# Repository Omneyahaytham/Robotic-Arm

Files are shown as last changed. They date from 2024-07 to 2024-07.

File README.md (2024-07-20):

# Robotic-Arm
Simulation of a robotic arm designed on solidworks and simulated on MATLAB and ROS. given a specific points that end effector must follow (Path planning)
used forward and inverse kinematics to minimize the error

Note:
you need robotic toolbox for this project.
need to know how to export solidwork design on matlab.

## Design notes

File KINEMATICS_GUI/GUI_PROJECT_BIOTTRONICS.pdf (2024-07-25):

### Mechatronics and robotics

Ahmed Mohamed Kotp | 7543
Omneya Haytham Mohamed | 7717
Faress Ahmed Mohamed Amin | 7925

# INTRO TO BIOTRONICS ASSIGNMENT

# GUI Assignment

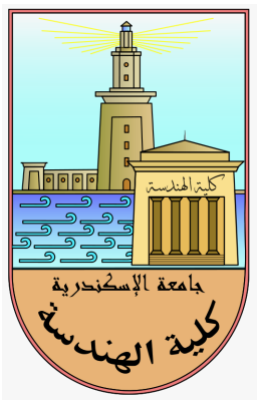
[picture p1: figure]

## GUI-Based Serial Link Kinematics Solver

## Objective:

The objective of this assignment is to develop a graphical user interface (GUI) application in

MATLAB for solving serial link kinematics problems. Students will design a user-friendly

interface that allows users to input serial link configurations and select the type of problem

(forward or inverse kinematics). They will then implement algorithms to solve the selected

problem type and display the final pose of the serial link robot.

### 1. GUI Design:

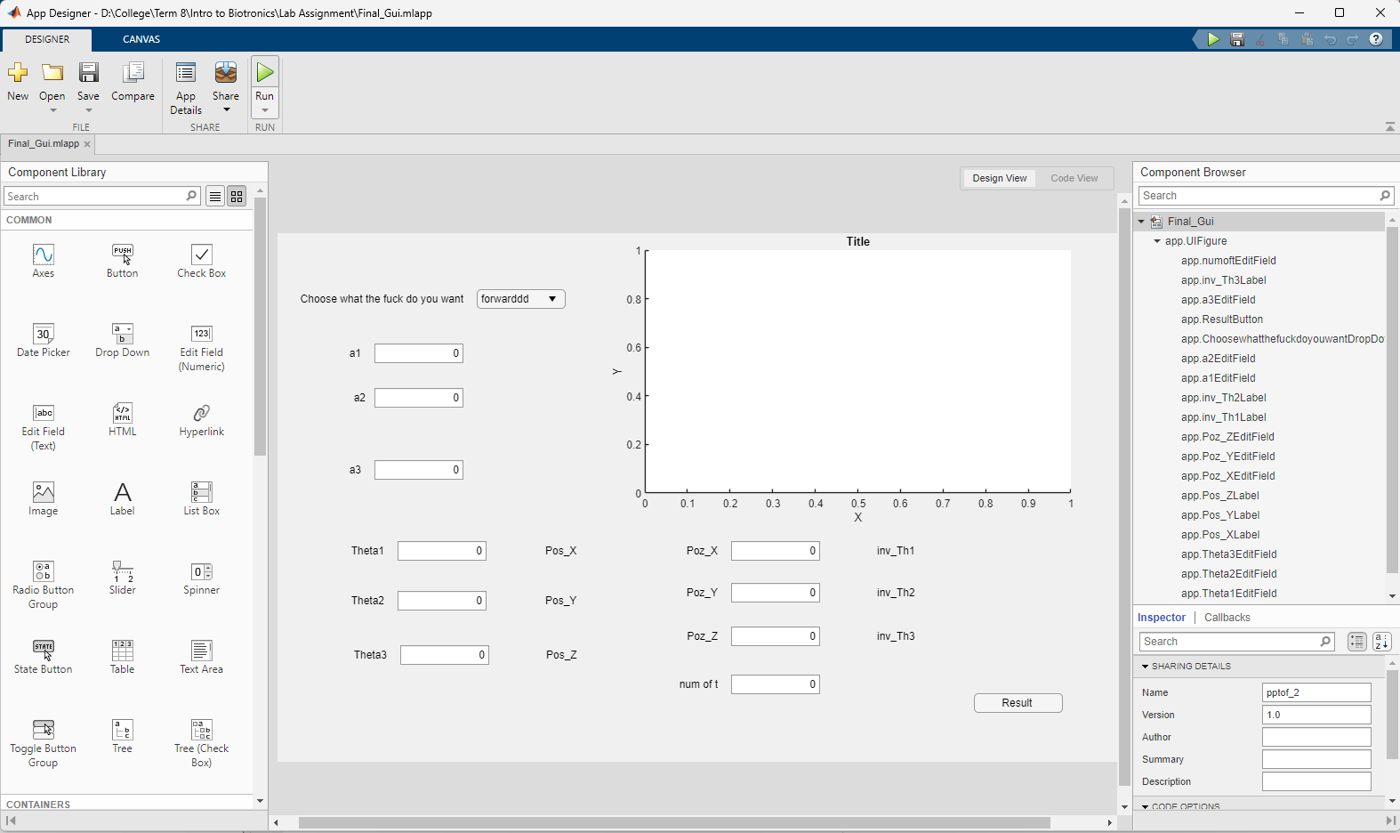
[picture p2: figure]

- First Here we have a drop-down menu to choose between Forward kinematics, Inverse

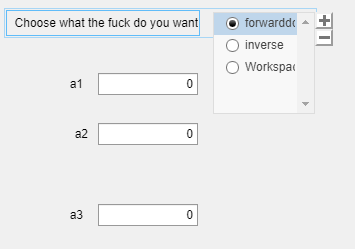
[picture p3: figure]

kinematics, and Workspace.

- Second, we have Edit fields for entering the three

link lengths of the robot.

- a1= length of first link
- a2= length of second link
- a3=length of third link

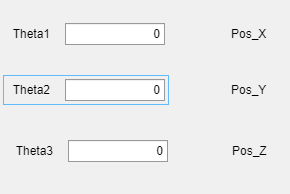
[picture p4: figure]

- For forward Kinematics:

we have the three joint angles input fields:

- Theta1
- Theta2
- Theta3

And corresponding X, Y, Z Positions for the end

effector.

- For Inverse Kinematics:

We have the input fields for X, Y, Z of end effector

(end effector position)

And the corresponding output thetas from the inverse

kinematics:

- Inv_Th1
- Inv_Th2
- Inv_Th3

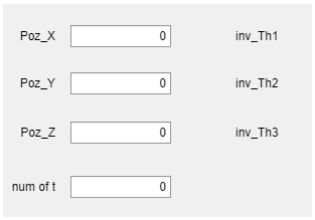
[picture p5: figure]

And we have number of iterations input field to minimize the error

### 2. Forward Kinematics Solver:

Code Logic:

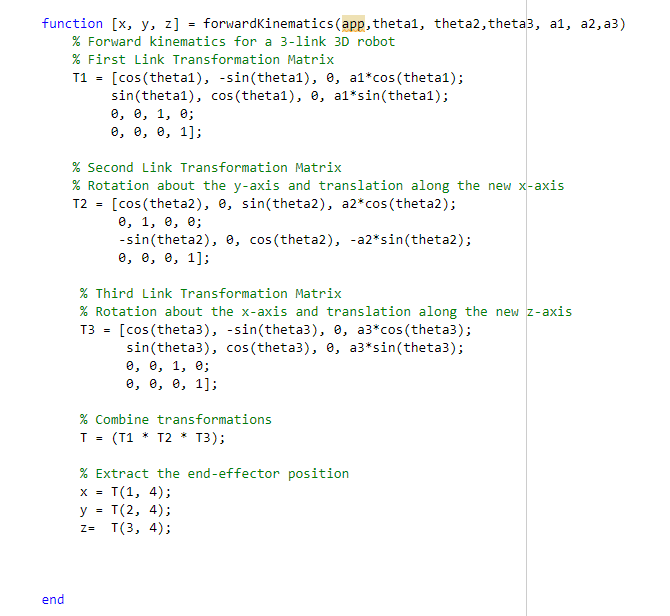
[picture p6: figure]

Here we calculate the transformation matrix of each link with respect to the previous Link,

then getting the end effector transformation matrix with respect to the base by multiplying

T1*T2*T3

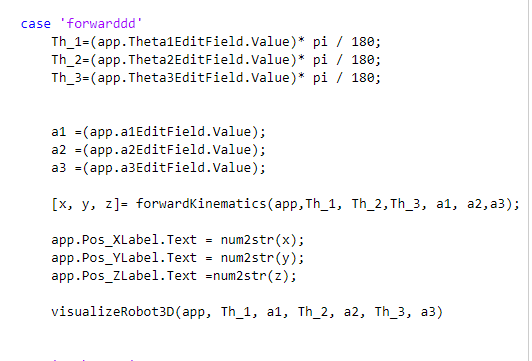
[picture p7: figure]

In case of choosing Forward kinematics from drop-down menu:

We will get the value entered of joint angles and links lengths in the input fields and use them in

the forward kinematics function to get the position of end effector and plotting the visualization of

the robot by a function named visualizationRobot3D.

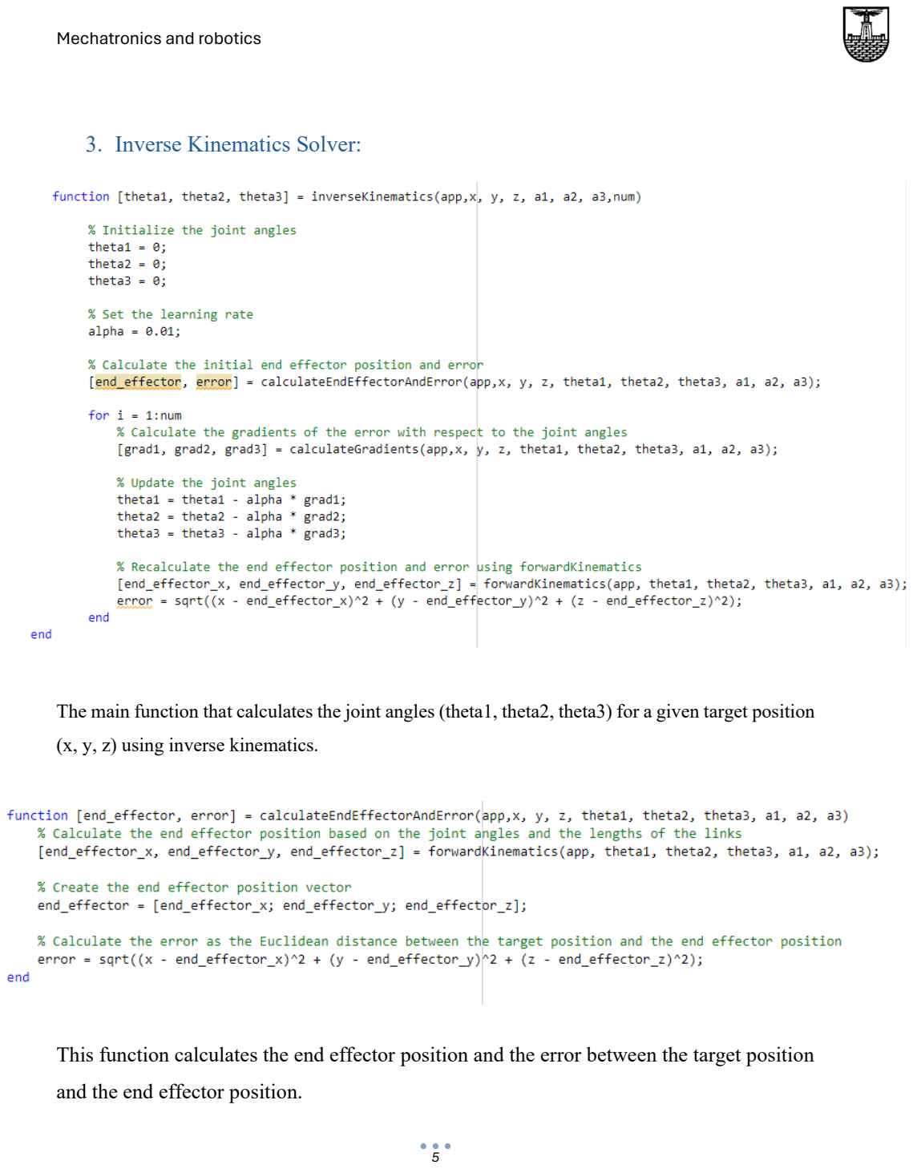
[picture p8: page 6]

### 3. Inverse Kinematics Solver:

The main function that calculates the joint angles (theta1, theta2, theta3) for a given target position

(x, y, z) using inverse kinematics.

This function calculates the end effector position and the error between the target position

and the end effector position.

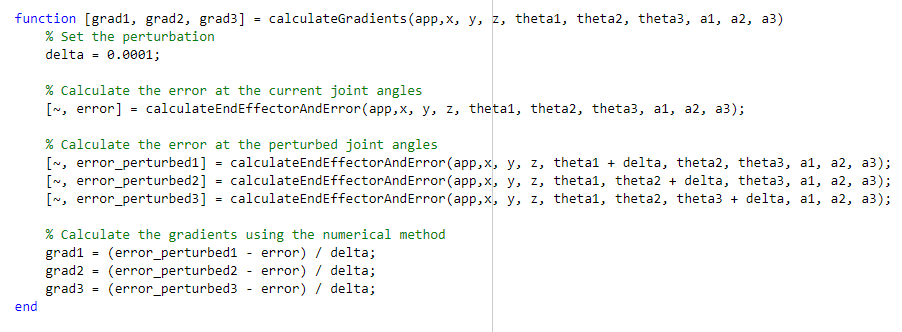
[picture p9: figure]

This function calculates the gradients of the error with respect to the joint angles using the

numerical method.

the Gradient refers to the slope or inclination of a line. However, in the context of

optimization and machine learning, a gradient is a vector that points in the direction of the

greatest rate of increase of a function. It’s calculated by taking the derivative of the function

with respect to each of its variables. The gradient is a crucial concept in optimization

algorithms because it provides guidance on how to adjust parameters to minimize or

maximize a particular function.

the gradient descent method is a first-order optimization algorithm used to find the

minimum of a function. It’s widely used in machine learning and deep learning for training

models, where the function to be minimized is often a loss function that calculates the

difference between the actual data and the model's predictions.

The gradient method works by iteratively adjusting the input of a function in the opposite

direction of the gradient (for minimization).

This is done until the algorithm converges to a local minimum. Here’s a step-by-step

process of how the gradient method works for minimization:

1. Initialize the input parameters.
2. Compute the gradient of the function at the current input.
3. Update the input by subtracting a fraction (known as the learning rate) of the

gradient from the current input:

4. xn+1=xn−α∇f(xn)
5. where xn is the current input,
6. α is the learning rate,
7. and ∇f(xn) is the gradient of the function at xn
8. Repeat the above steps until the change in the function output is below a certain

threshold or a maximum number of iterations is reached.

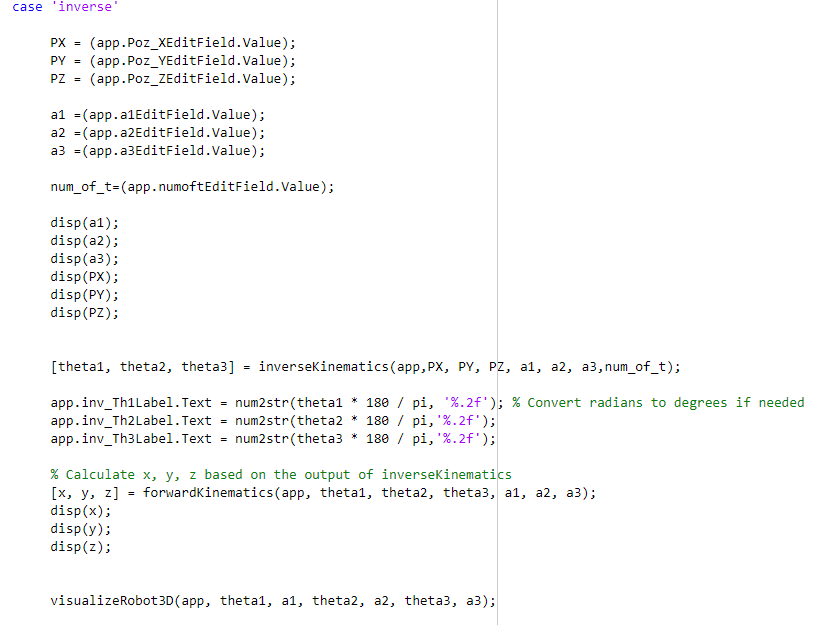
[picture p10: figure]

### 4. Robot workspace drawing:

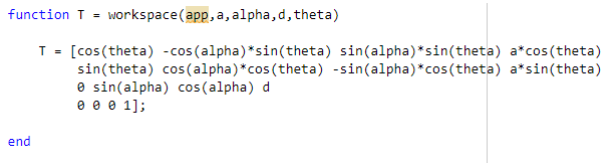
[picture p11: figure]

This is a function that have the transformation matrix we substitute in it with each theta and a

- function out = arr2Rad(app,A):
- This line defines the function arr2Rad with two input arguments: app and A.
- A is the array of angles that we want to convert from degrees to radians.
- The function will return the output as out.
- out = arrayfun(@(angle) deg2rad(angle), A);:
- This line uses the arrayfun function to apply the conversion operation to each element of

the array A.

- arrayfun applies the function @(angle) deg2rad(angle) to each element of A.
- @(angle) is an anonymous function that takes an input argument angle.
- deg2rad(angle) is a built-in MATLAB function that converts an angle from degrees to

radians.

- The result of arrayfun is assigned to the variable out, which becomes the output of the

arr2Rad function.

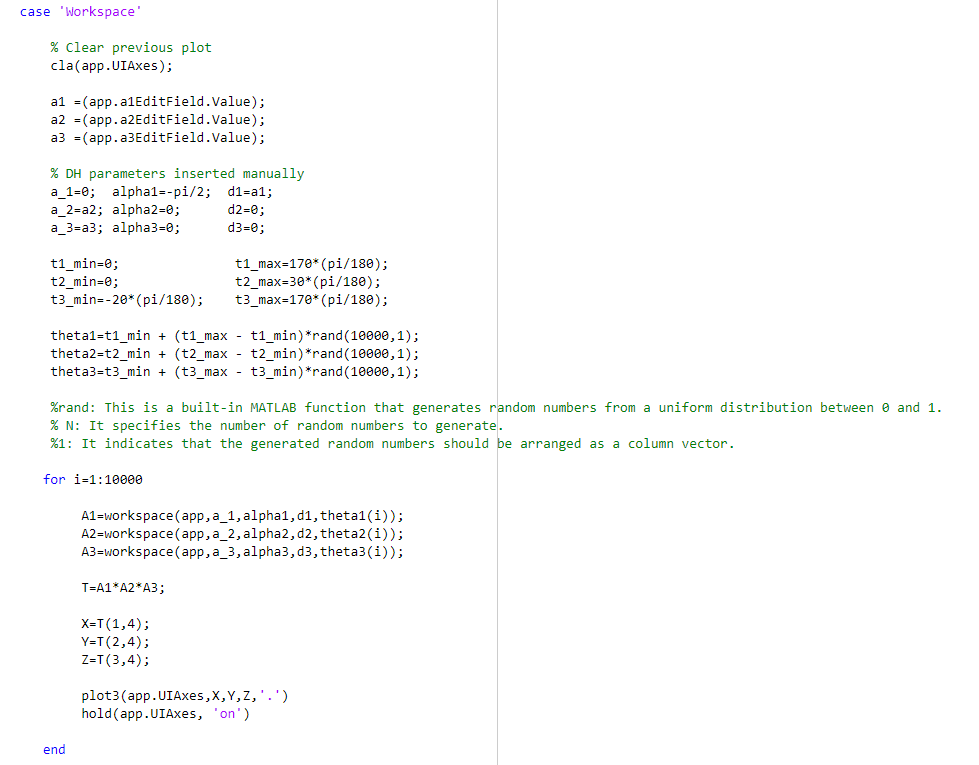
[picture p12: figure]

- cla(app.UIAxes):

This line clears the previous plot from the UIAxes object, which is likely a MATLAB GUI

component used for displaying plots.

- The following lines assign values from GUI input fields.
- a1 = app. a1EditField.Value
- a2 = app. a2EditField.Value
- a3 = app. a3EditField.Valuet

- Then manually set the Denavit-Hartenberg (DH) parameters for the robotic arm. These

parameters describe the kinematic properties of each joint in the arm. Specifically:

- a_1, alpha1, d1 represent the parameters for the first joint.
- a_2, alpha2, d2 represent the parameters for the second joint.
- a_3, alpha3, d3 represent the parameters for the third joint.
- define the minimum and maximum joint angles:
- t1_min, t1_max
- t2_min, t2_max
- t3_min, t3_max

for each joint of the robotic arm.

- The theta1, theta2, and theta3 variables are generated using the rand function to create 10,000

random joint angle configurations within the specified ranges.

- The subsequent for loop iterates over each random joint angle configuration.
- Within the loop, the workspace function is called three times with different joint parameters

and the current random joint angles:

- theta1(i)
- theta2(i)
- theta3(i))

to calculate the transformation matrices A1, A2, and A3 for each joint.

- The transformation matrices A1, A2, and A3 are multiplied together to obtain the overall

transformation matrix T representing the end-effector pose.

- The X, Y, and Z coordinates of the end-effector position are extracted from the transformation

matrix T.

- The plot3 function is used to plot the X, Y, and Z coordinates on the UIAxes object as

individual data points in a three-dimensional plot.

- The hold function is used to ensure that subsequent plots are overlaid on the same figure.
- The loop continues until all 10,000 random joint angle configurations have been processed.

### 5. Testing and Validation:

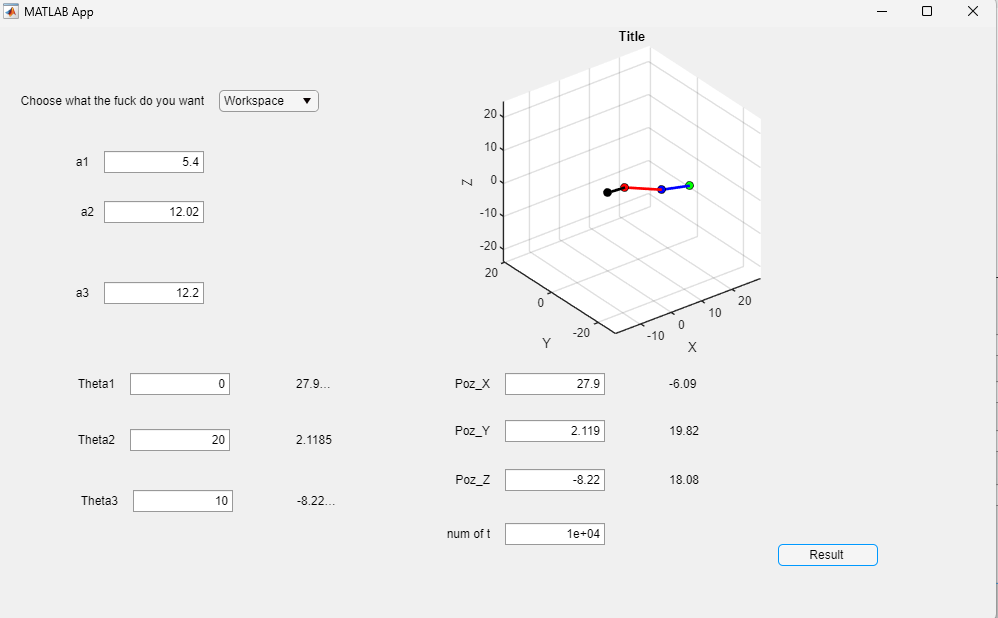
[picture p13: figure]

### A. GUI

Here is and example using the GUI we created with links lengths:

✓ a1 = 5.4

✓ a2 = 12.02

✓ a3 = 12.2

1. In forward Kinematics:

Joint revolute angles:

✓ Theta1 = 0 degrees

✓ Theta2 = 20 degrees

✓ Theta3 = 10 degrees

The output of end effector position:

✓ X = 27.9

✓ Y = 2.1185

✓ Z = -8.22

2. Inverse Kinematics:

The input is the same as the output from forward kinematics to check the error.

Input end effector position:

✓ X = 27.9

✓ Y = 2.1185

✓ Z = -8.22

Output revolute angles of each joint:

✓ Inv_Theta1 = -6.09

✓ Inv_Theta2 = 19.82

✓ Inv_Theta3 = 18.08

As observed, there is error, but the error is small.

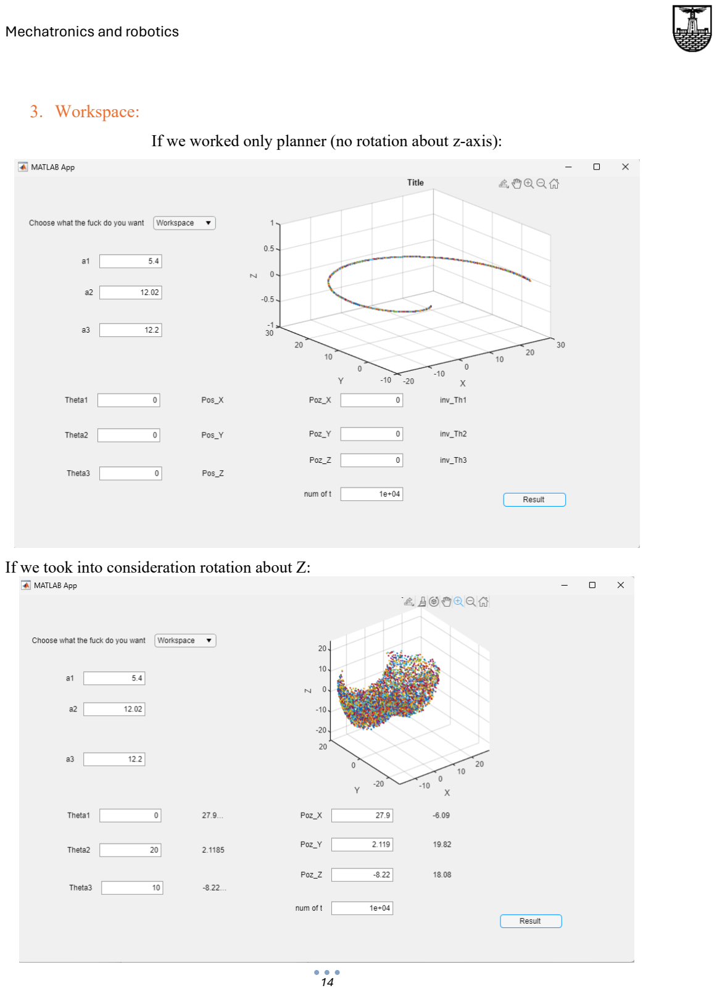
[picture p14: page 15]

3. Workspace:

If we worked only planner (no rotation about z-axis):

If we took into consideration rotation about Z:

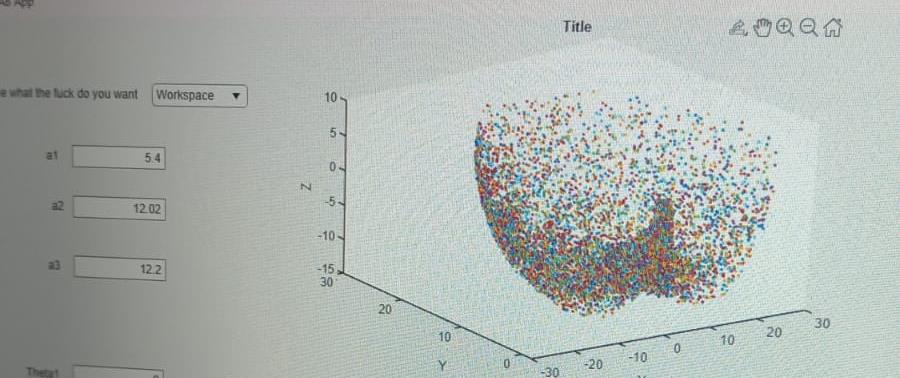
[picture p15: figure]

### B. Peter Cork:

1. In forward Kinematics:

Code:

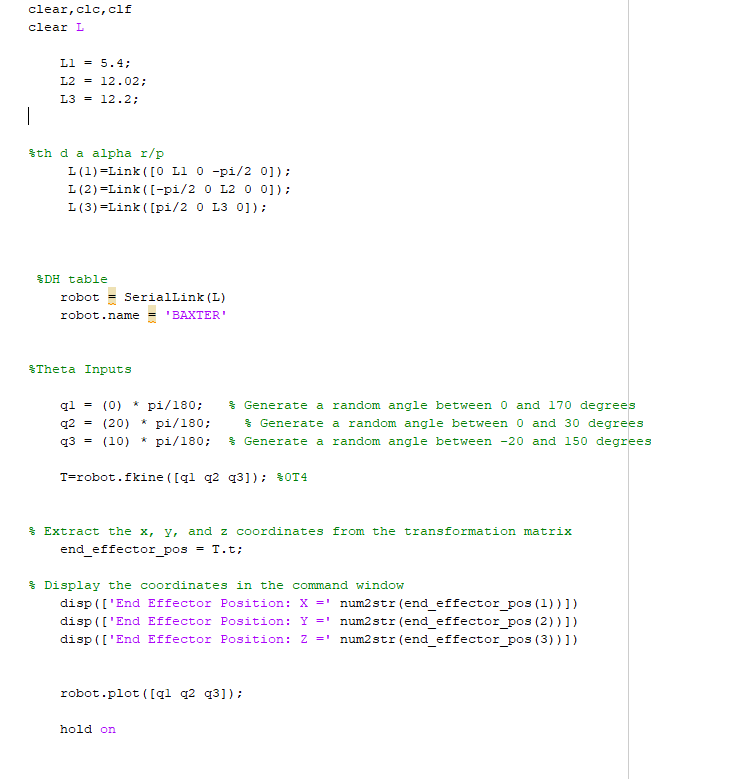
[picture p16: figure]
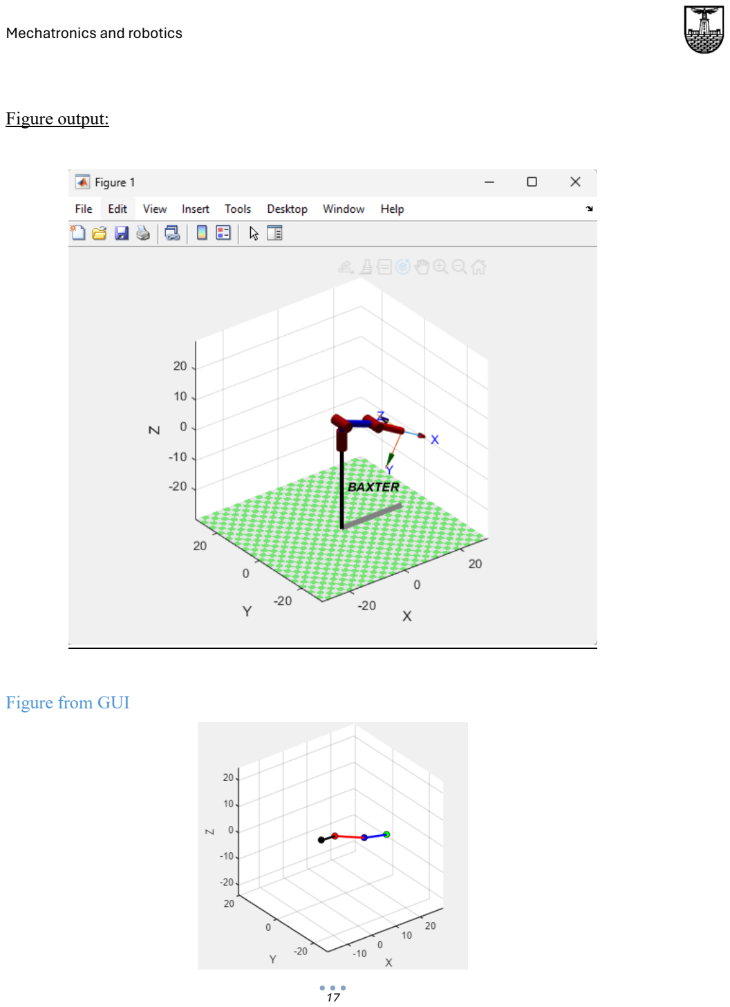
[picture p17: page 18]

Figure output:

Figure from GUI

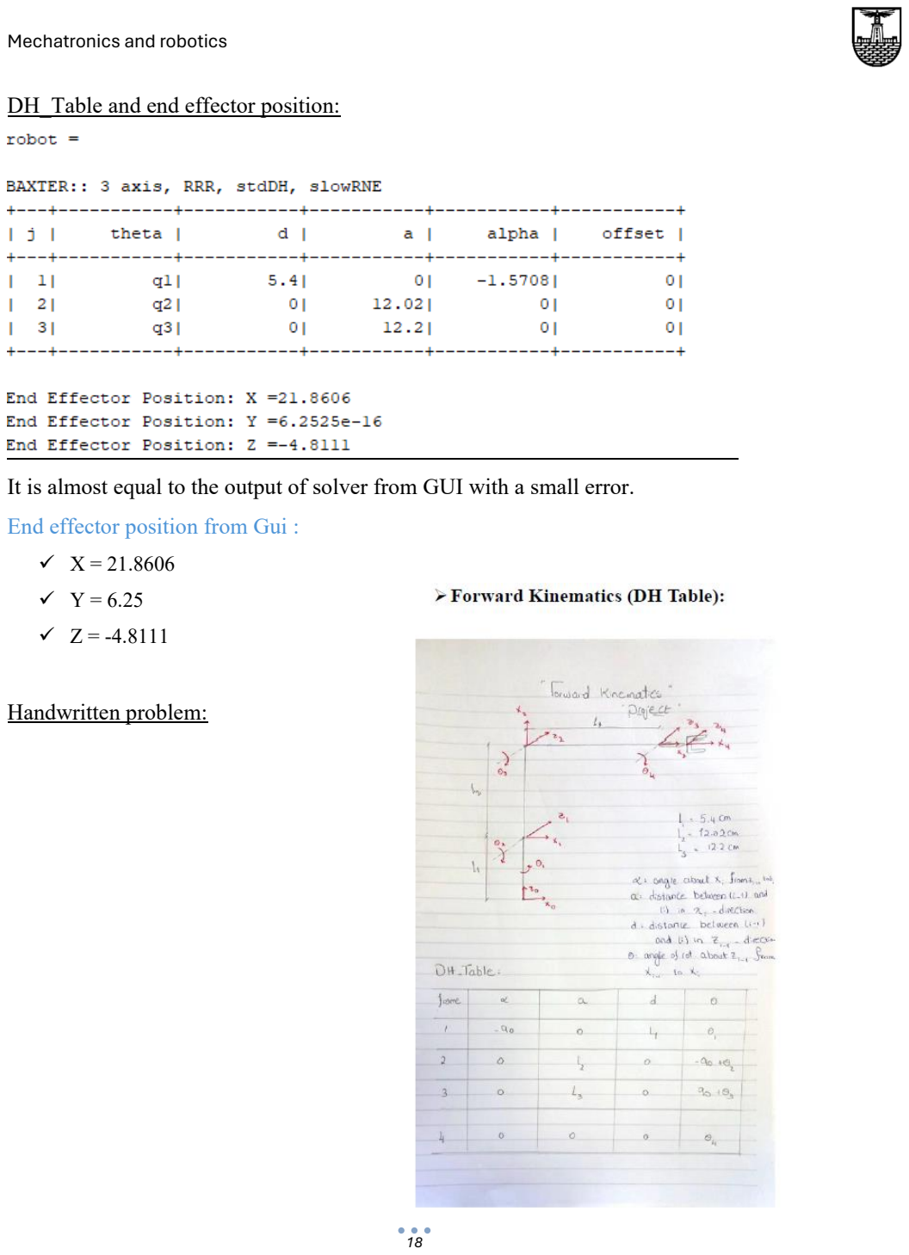
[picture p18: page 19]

DH_Table and end effector position:

It is almost equal to the output of solver from GUI with a small error.

End effector position from Gui :

✓ X = 21.8606

✓ Y = 6.25

✓ Z = -4.8111

Handwritten problem:

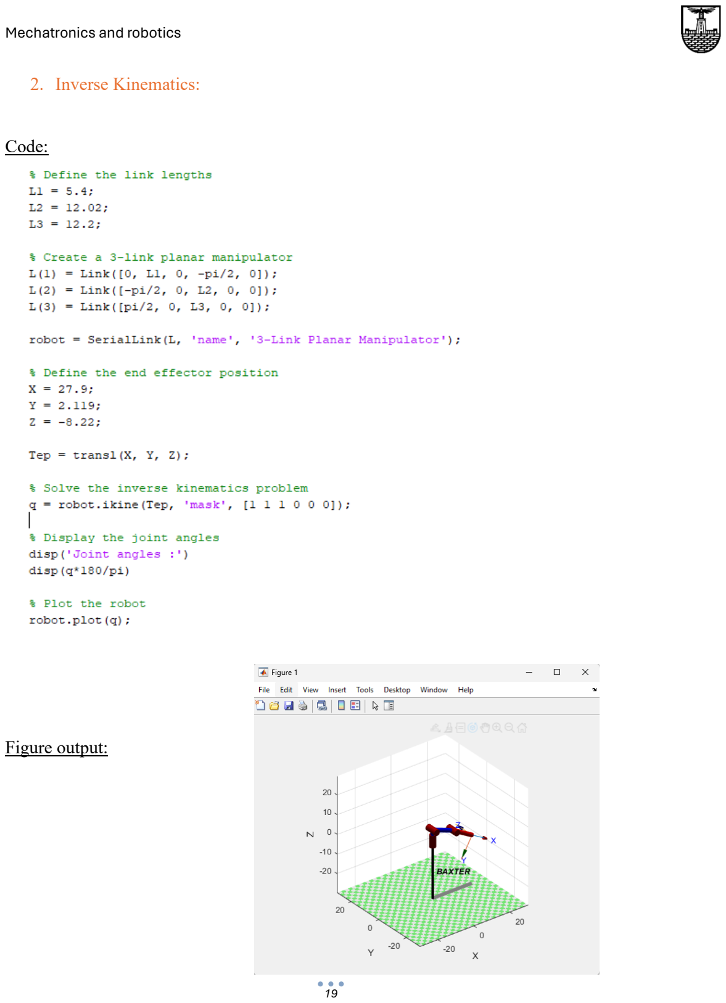
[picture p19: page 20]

2. Inverse Kinematics:

Code:

Figure output:

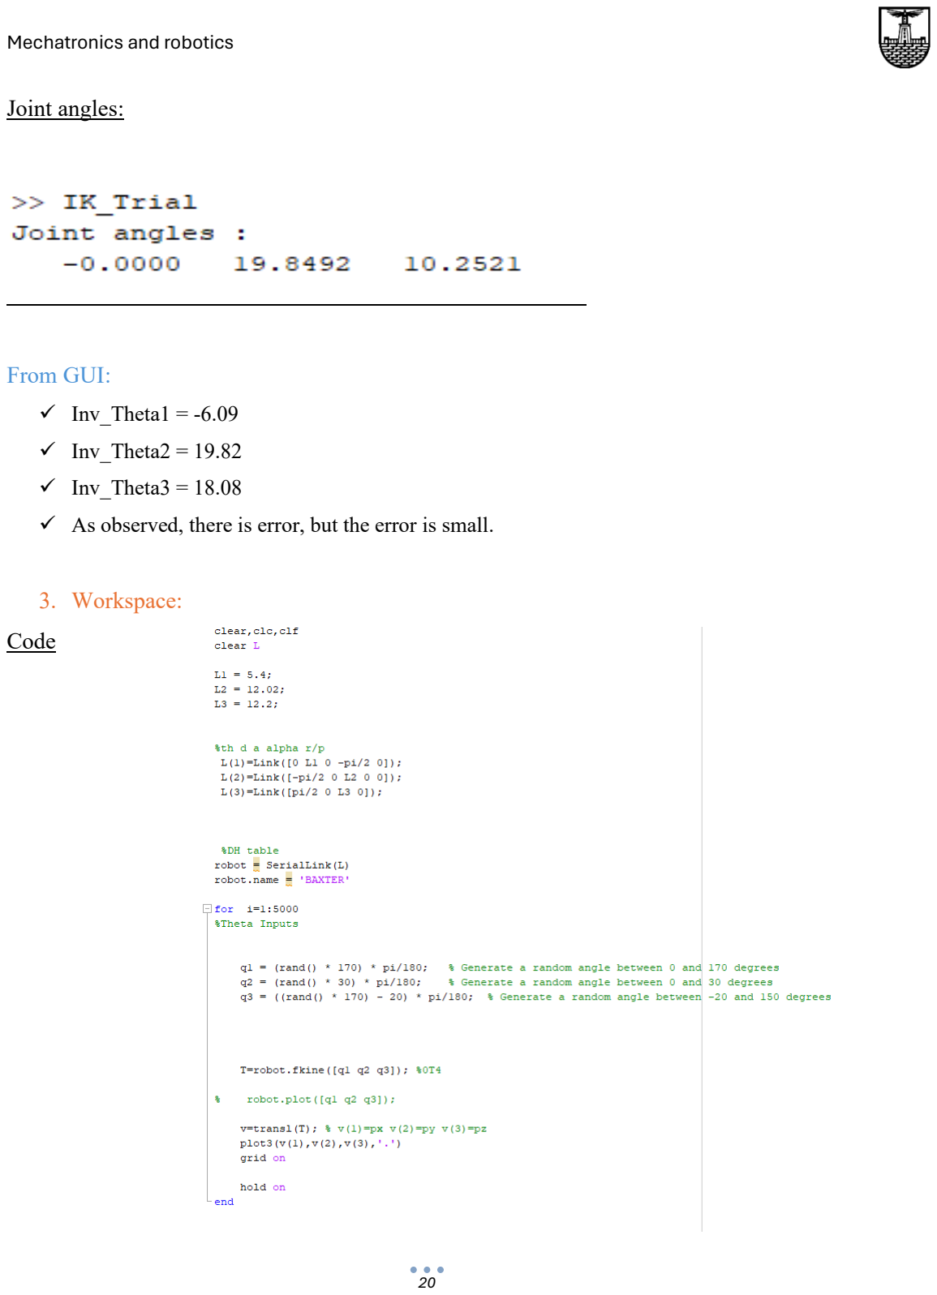
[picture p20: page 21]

Joint angles:

From GUI:

✓ Inv_Theta1 = -6.09

✓ Inv_Theta2 = 19.82

✓ Inv_Theta3 = 18.08

✓ As observed, there is error, but the error is small.

3. Workspace:

Code

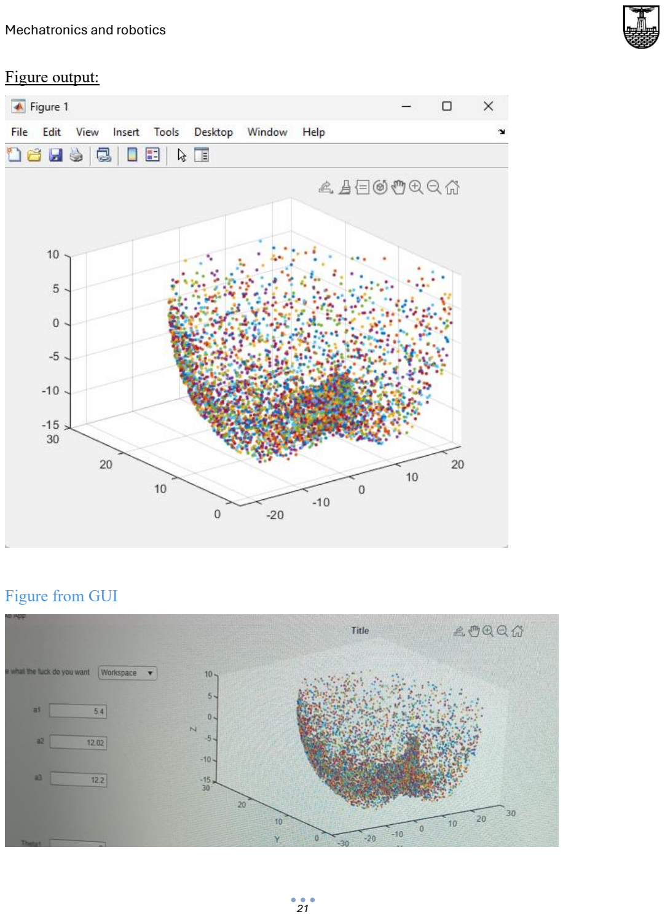
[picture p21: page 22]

Figure output:

Figure from GUI

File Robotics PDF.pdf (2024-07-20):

Faculty of Engineering Alexandria University | Mechatronics

# Robotic Arm Project

Due Tuesday 12 December 2023

### Represented by:

Omneya Haytham Mohamed Ezz Eldin | 7717
Mohamed Hussein Mohamed Elzoheiry | 7818
Faress Ahmed Mohamed Amin | 7925
Ahmed Mohamed Kotp | 7543
Ahmed Reda | 7417

## Mechatronics

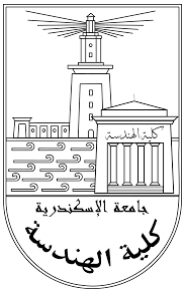
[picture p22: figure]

## ➢SolidWorks Design:

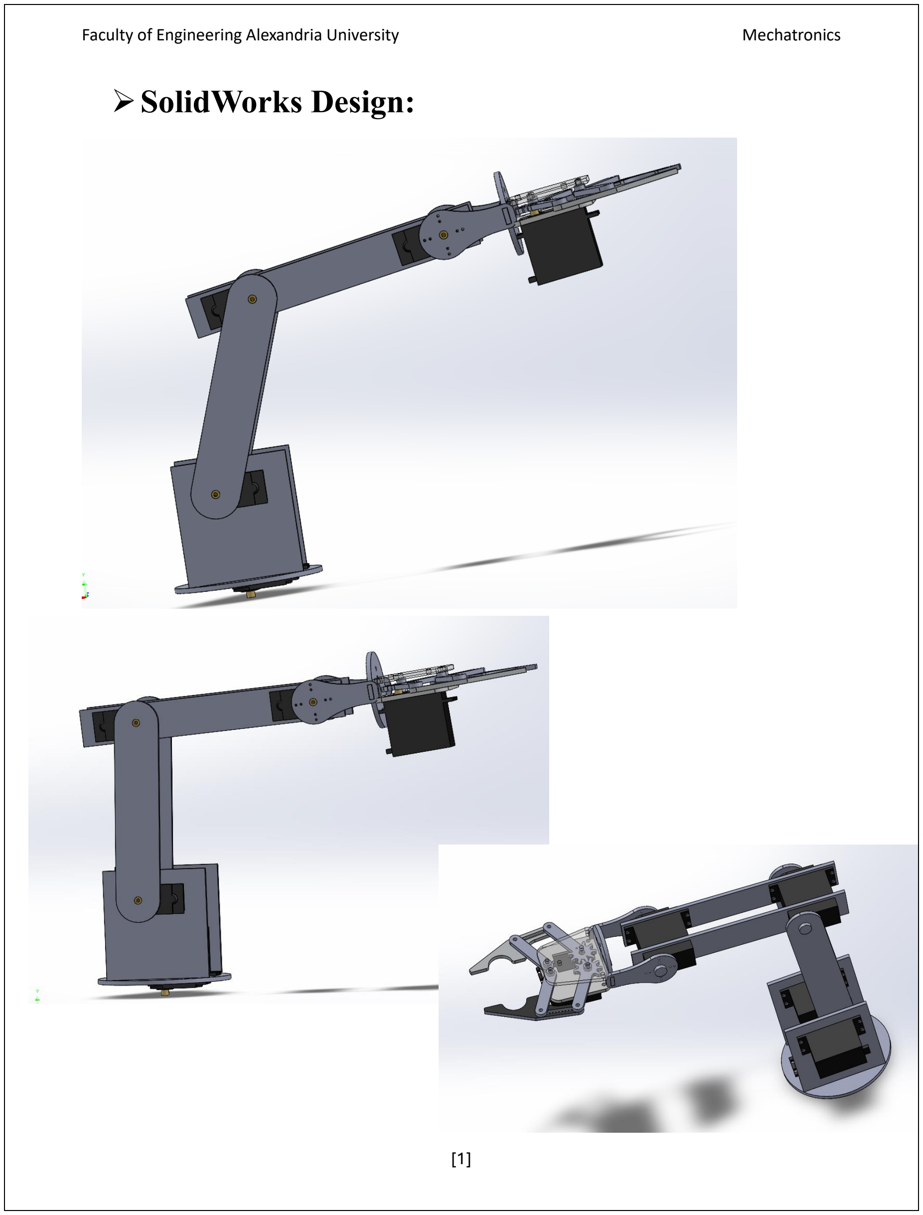
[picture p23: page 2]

## ➢Forward Kinematics (DH Table):

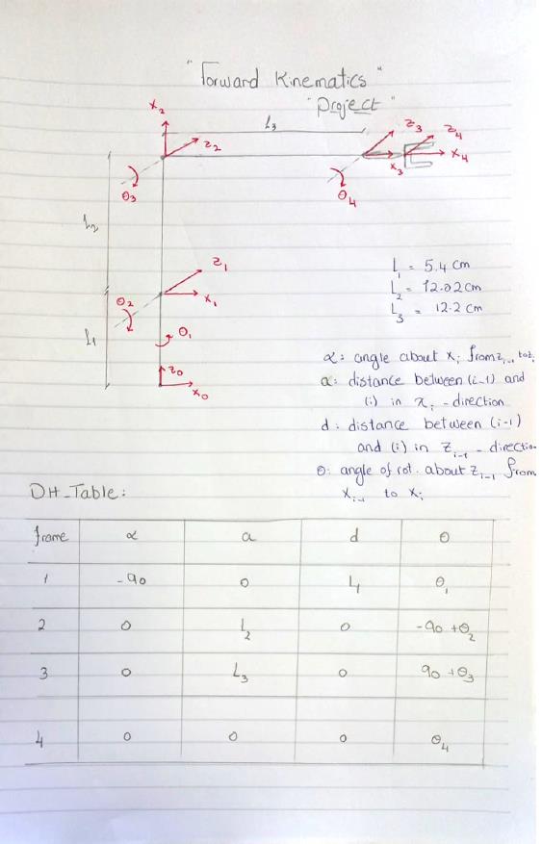
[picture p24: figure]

## ➢Simscape Model:


## ➢Workspace:

- Angle of rotation of each link Approximately.

Link1: 170 degrees.

Link2: 30 degrees.

Link3: 170 degrees.

Link4: 120 degrees.



If we want to draw a specific position, we can add this line:

%robot.plot([q1 q2 q3 q4]);

And substitute with the desired q value.

For example:

If we want:

q1 = 0,

q2 = 20*(pi/180),

q3 = 0,

q4 = 0

- The Code:


- | Robot | position:
- The output DH_Table from the code:

The previous robot design was complex and have a lot of errors when trying to work on MATLAB due to servo motors.

And another problem is that MATLAB see the parallel links as more than one link, so it is not considered as one link.

Therefore, we had to modify the SolidWorks design to a simple model with rigid links.

## ➢New SolidWorks Design:


## ➢New Simscape Model:


## ➢For the Robot to follow a specific trajectory:


First, we must make the rigid bodytree variable for the robot using the following command:

We generated a signal (X, Y, Z) using signal builder, the positions X, Y, Z

output of signal builder is the input to the inverse kinematics block. This block

gives us the angles of the joints passed to the robot.

The sensed position from robot passed to the forward kinematics block to give

back the position of end effector and compare it with the signal we made.


### Forward Kinematics block:

We must specify the rigid body tree, Base, and End effector.


### Inverse Kinematics Block:

Here we also must specify the rigid body tree and the end effector only.

### Signal Builder:


Instead of making a random signal, there is several trajectory blocks in

MATLAB robotic toolbox:

### 1. Polynomial trajectory:

At start we generated trajectory,providing that trajectory to the inverse

kinematics block.

Inverse kinematic block converts that trajectory into joint angles which is

provided to the robot.

Then measuring the joint angles of the robot giving those joint angles to the

forward kinematics block, the forward kinematics block convert these angles

back to the end effector positions.

Therefore, we are comparing the trajectory on which the robot was moving

with the trajectory that we were providing using the scope.


We used cubic polynomial.

For this type we had to give it waypoints that the robot must follow, and time taken for the robot to reach each waypoint.

Here are the waypoints:

Scope output:


The first graph is the output X, Y, Z from the forward kinematics.

The second graph is the output from our trajectory.

And the third graph shows the velocities in X, Y, Z.

As we can see here there is error between the position from trajectory and forward kinematics, this error is handled by a controller (PID) to eliminate the error.

### 2. Trapezoidal velocity profile:

Used if robot moves in linear motion, want to transverse in straight line.

- Move with constant acceleration.
- Achieve a certain velocity.
- Move with that constant velocity for some time.
- Then decelerates again.

We need to do the same comparison of the position to the velocities; therefore, we will use

Jacobian.

## Jacobian:

Using the get Jacobian block from robotic toolbox:

This Jacobian matrix will be 6*n matrix.

6 is for the 6 velocities we are going to get; the first three

velocities are the angular velocities, and the last three

velocities will be the linear velocities.

The columns of this Jacobian matrix will correspond to

the number of joints we have.

There is a huge error in the values due to the error coming from the inverse kinematics

block, therefore, to reduce this error by decrease the tolerance.


For velocity comparison:

Scope output:

Visualizing the angles from inverse kinematics:

To take the output angles from the inverse kinematics block and send the angles to the hardware Arduino package is used in MATLAB Simulink.


Servo write is used to send the output on the servo motor in the hardware by defining the pin of the signal.

We used Data Type Conversion Block to round the output angle an send it as an integer, as the servo write block only take integer values.

# Using ROS

For the controlling of the robot arm we have used Moveit.

### MoveIt builds on the ROS messaging and build systems and utilizes some of the common tools in ROS like the ROS Visualizer (Rviz) and the ROS robot

format (URDF).
Moveit runs on the top of ROS (robot operating system).

### ROS is an open-source meta-operating system for robots that provides low-level functionality like a build system, message passing, device drivers and

some integrated capabilities like navigation.

### First we simplify the design of the real robotic arm to make the URDF

exportation easier.


### Then after configuring the URDF file , we imported it in Moveit setup assistant and we defined specific planning groups and poses for the robotic arm to


follow.

### Then we generated our package which contain all the needed launch files which run Gazebo, Rviz, RosControl tools which helps us in our simulation

and control of the robotic arm.


### For the interfacing with the hardware of the robotic arm and send the angles to the servo motors according to the motion planning done by Moveit we have used ROSSERIAL with Arduino mega and we make the real robotic arm move

like the simulation in Gazebo and Rviz.
Finally, this is the rqt graph of our system.

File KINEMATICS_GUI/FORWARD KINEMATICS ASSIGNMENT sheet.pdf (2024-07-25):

## Mechatronics and robotics

Ahmed Mohamed Kotp | 7543
Omneya Haytham Mohamed | 7717
Faress Ahmed Mohamed Amin | 7925

# INTRO TO BIOTRONICS ASSIGNMENT

# Forward Kinematics Sheet


# FORWARD KINEMATICS ASSIGNMENT


# - Forward Kinematics Equation:


# - MATLAB Code:

clear,clc

% Ensure you have the Symbolic Math Toolbox installed and available syms theta1 theta2 theta3 real;
syms d1 a1 real;
syms d2 a2 real;
syms d3 a3 real;
syms alpha1 alpha2 alpha3 real;

% Assume some typical values for d, a, alpha or leave them as symbols % Link 1
alpha1 =0;
a1_val = 0;
d1 = -a1;
theta1_val = theta1;

% Link 2
alpha2 = 0;
a2_val = 0;
d2 = -a2;
theta2_val = theta2+(pi/2);

% Link 3
alpha3 = 0;
a3_val = 0;
d3 = -a3;
theta3_val = theta3-(pi/2);

% Compute transformation matrices for each link A1 = DhTable(a1_val, alpha1, d1,theta1_val); A2 = DhTable(a2_val, alpha2, d2,theta2_val);
A3 = DhTable(a3_val, alpha3, d3,theta3_val);

% Compute the overall transformation matrix from base to end-effector T = A1 * A2 * A3;

T = simplify(T);

% Display results
disp('0T1 = A1 = ');
disp(A1);
disp('1T2 = A2 = ');
disp(A2);

disp('2T3 = A3 = ');
disp(A3);
disp('0T3 = ');
disp(T);

function T = DhTable(a,alpha,d,theta)
% Define the DH transformation matrix as an anonymous function DHMatrix = [cos(theta) -cos(alpha)*sin(theta) sin(alpha)*sin(theta) a*cos(theta);
sin(theta) cos(alpha)*cos(theta) -sin(alpha)*cos(theta) a*sin(theta);
0 sin(alpha) cos(alpha) d;
0 0 0 1];

T = DHMatrix;
end

# - Output:


# - Forward Kinematics Equation:


# - MATLAB Code:

clear,clc

% Ensure you have the Symbolic Math Toolbox installed and available syms theta1 theta2 theta3 real;
syms d1 a1 real;
syms d2 a2 real;
syms d3 a3 real;
syms alpha1 alpha2 alpha3 real;

% Assume some typical values for d, a, alpha or leave them as symbols % Link 1
alpha1 =pi/2;
a1_val = 0;
d1_val = d1;
theta1_val = 0;

% Link 2
alpha2 = 0;
a2_val = 0;
d2_val = d2;
theta2_val = 0;

% Compute transformation matrices for each link A1 = DhTable(a1_val, alpha1, d1_val,theta1_val);
A2 = DhTable(a2_val, alpha2, d2_val,theta2_val);

% Compute the overall transformation matrix from base to end-effector T = A1 * A2 ;

T = simplify(T);

% Display results
disp('0T1 = A1 = ');
disp(A1);

disp('1T2 = A2 = ');
disp(A2);

disp('0T2 = ');
disp(T);

function T = DhTable(a,alpha,d,theta)
% Define the DH transformation matrix as an anonymous function DHMatrix = [cos(theta) -cos(alpha)*sin(theta) sin(alpha)*sin(theta) a*cos(theta);
sin(theta) cos(alpha)*cos(theta) -sin(alpha)*cos(theta) a*sin(theta);
0 sin(alpha) cos(alpha) d;
0 0 0 1];

T = DHMatrix;
end

# - Output:

0T1 = A1

[1, 0, 0, 0]
[0, 0, -1, 0]
[0, 1, 0, d1]
[0, 0, 0, 1]

1T2 = A2 =
[1, 0, 0, 0]
[0, 1, 0, 0]
[0, 0, 1, d2]
[0, 0, 0, 1]

0T2 =

[1, 0, 0, 0]
[0, 0, -1, -d2]
[0, 1, 0, d1]
[0, 0, 0, 1]


# - Forward Kinematics Equation:


# - Output:


# - Forward Kinematics Equation:


# - Output:


# - Forward Kinematics Equation:


# - Output:


T =
[cos(theta1)*cos(theta2)*cos(theta3) - cos(theta1)*sin(theta2)*sin(theta3),
- cos(theta1)*cos(theta2)*sin(theta3) - cos(theta1)*cos(theta3)*sin(theta2), sin(theta1),

## a2*cos(theta1)*cos(theta2) + a3*cos(theta1)*cos(theta2)*cos(theta3) -a3*cos(theta1)*sin(theta2)*sin(theta3)]

[cos(theta2)*cos(theta3)*sin(theta1) - sin(theta1)*sin(theta2)*sin(theta3),
- cos(theta2)*sin(theta1)*sin(theta3) - cos(theta3)*sin(theta1)*sin(theta2), -cos(theta1),

## a2*cos(theta2)*sin(theta1) + a3*cos(theta2)*cos(theta3)*sin(theta1) -a3*sin(theta1)*sin(theta2)*sin(theta3)]

[cos(theta2)*sin(theta3) + cos(theta3)*sin(theta2),

## cos(theta2)*cos(theta3) -sin(theta2)*sin(theta3), 0, a1 + a2*sin(theta2) + a3*cos(theta2)*sin(theta3) + a3*cos(theta3)*sin(theta2)]

[0, 0, 0, 1]


# - Forward Kinematics Equation:


# - Output:


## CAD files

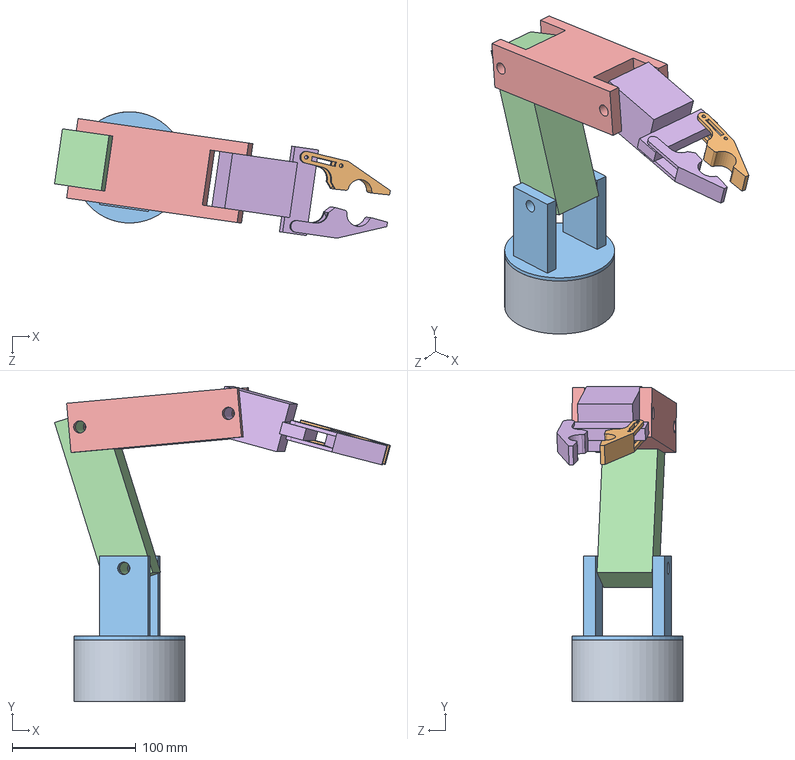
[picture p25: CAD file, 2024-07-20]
SolidWorks Design/New_assembly.SLDASM
271.9 x 255.3 x 102.3 mm
Base_link
End Effector
Link1
Link2
Link3
Link4

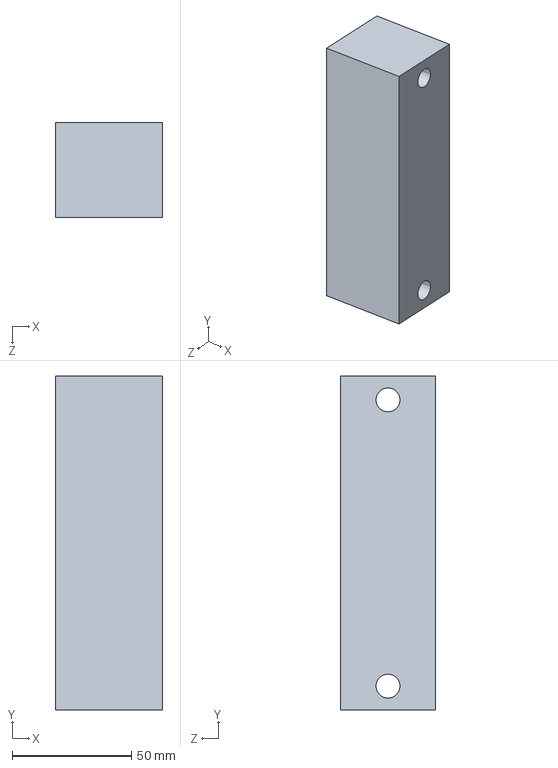
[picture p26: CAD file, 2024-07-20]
Simscape Model/Exported/Link2_Default_sldprt.STEP
45.0 x 140.0 x 40.0 mm

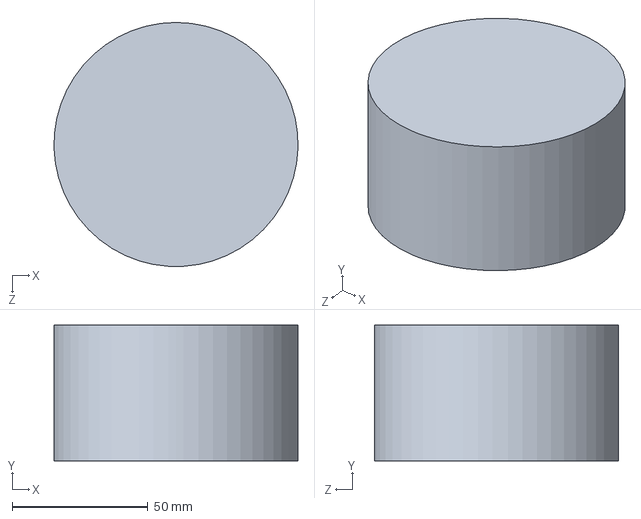
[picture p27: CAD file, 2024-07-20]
SolidWorks Design/Base_link.SLDPRT
90.0 x 50.0 x 90.0 mm

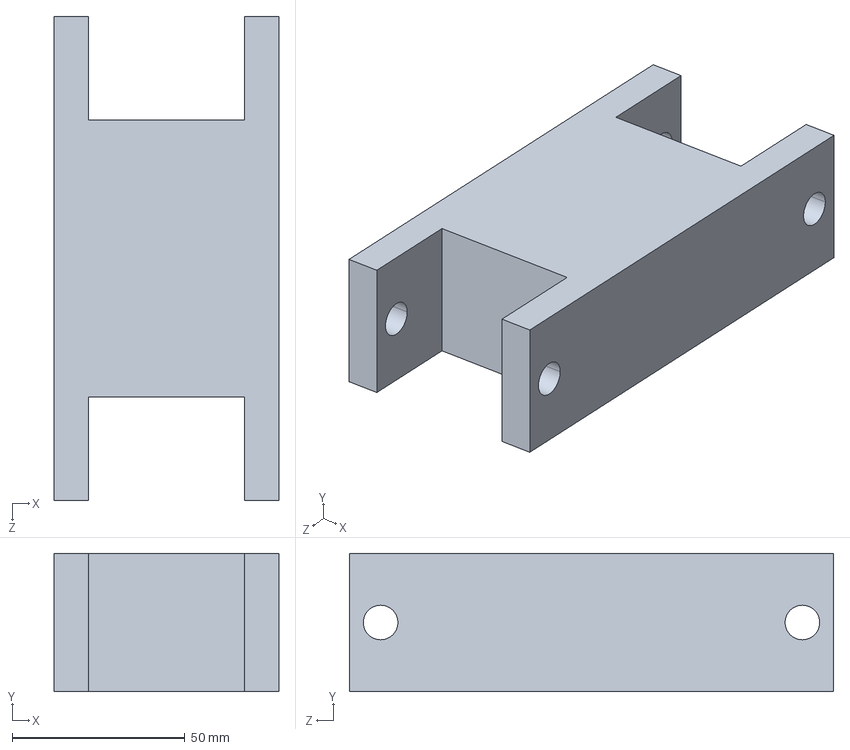
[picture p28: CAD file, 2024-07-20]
Simscape Model/Exported/Link3_Default_sldprt.STEP
65.0 x 40.0 x 140.0 mm

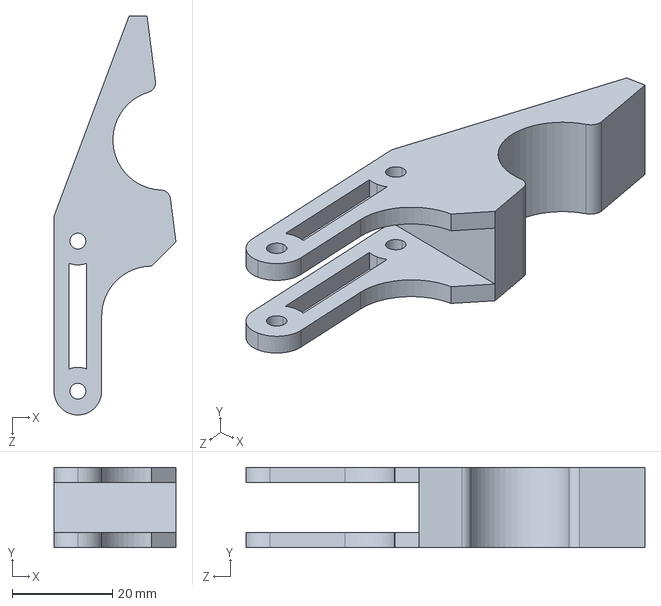
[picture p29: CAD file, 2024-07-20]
Simscape Model/Exported/End Effector_Default_sldprt.STEP
24.4 x 16.0 x 79.8 mm

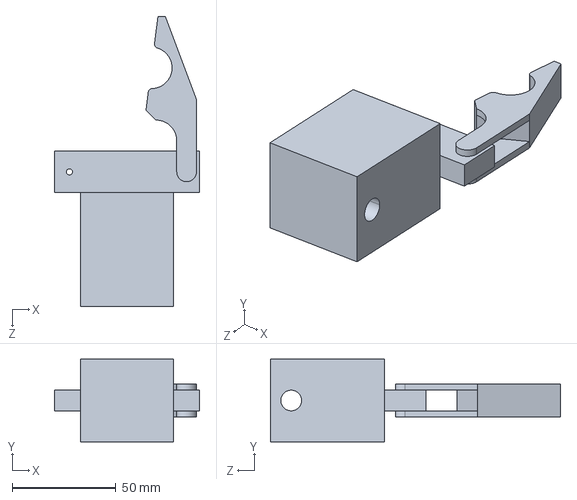
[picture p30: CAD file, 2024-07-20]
Simscape Model/Exported/Link4_Default_sldprt.STEP
70.0 x 40.0 x 140.0 mm

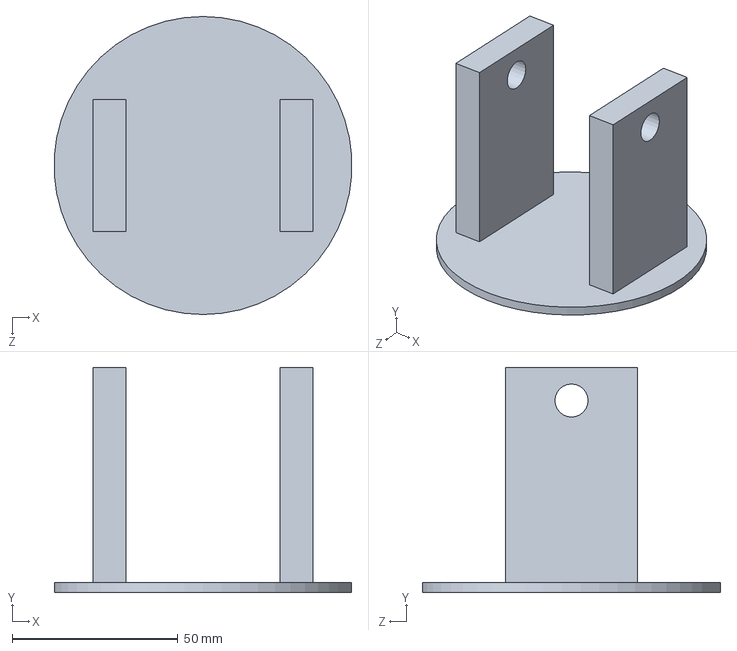
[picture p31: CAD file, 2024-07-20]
SolidWorks Design/Link1.SLDPRT
89.8 x 68.0 x 90.0 mm

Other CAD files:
SolidWorks Design/Link3.SLDPRT
SolidWorks Design/Link2.SLDPRT
SolidWorks Design/Link4.SLDPRT
SolidWorks Design/End Effector.SLDPRT

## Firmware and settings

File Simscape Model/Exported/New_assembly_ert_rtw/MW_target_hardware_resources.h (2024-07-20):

#ifndef PORTABLE_WORDSIZES
#ifdef __MW_TARGET_USE_HARDWARE_RESOURCES_H__
#ifndef __MW_TARGET_HARDWARE_RESOURCES_H__
#define __MW_TARGET_HARDWARE_RESOURCES_H__

#define MW_MULTI_TASKING_MODE 0
#include "MW_ArduinoHWInit.h"
#include "arduinoAVRScheduler.h"

#define MW_USECODERTARGET 1
#define MW_TARGETHARDWARE Arduino Mega 2560
#define MW_CONNECTIONINFO_SERIAL_IPADDRESS codertarget.arduinobase.registry.getLoopbackIP;
#define MW_CONNECTIONINFO_SERIAL_PORT 17725
#define MW_CONNECTIONINFO_SERIAL_VERBOSE 0
#define MW_CONNECTIONINFO_TCPIP_IPADDRESS codertarget.arduinobase.internal.getExternalModeMexArgs('Ethernet')
#define MW_CONNECTIONINFO_TCPIP_PORT 17725
#define MW_CONNECTIONINFO_TCPIP_VERBOSE 0
#define MW_CONNECTIONINFO_WIFI_IPADDRESS codertarget.arduinobase.internal.getExternalModeMexArgs('Wifi')
#define MW_CONNECTIONINFO_WIFI_PORT 17725
#define MW_CONNECTIONINFO_WIFI_VERBOSE 0
#define MW_CONNECTIONINFO_XCPONSERIAL_BAUDRATE codertarget.arduinobase.registry.getBaudRate
#define MW_CONNECTIONINFO_XCPONSERIAL_COMPORT codertarget.arduinobase.internal.getExternalModeMexArgs('Serial')
#define MW_CONNECTIONINFO_XCPONSERIAL_VERBOSE 0
#define MW_CONNECTIONINFO_XCPONTCPIP_IPADDRESS codertarget.arduinobase.internal.getExternalModeMexArgs('Ethernet')
#define MW_CONNECTIONINFO_XCPONTCPIP_PORT 17725
#define MW_CONNECTIONINFO_XCPONTCPIP_VERBOSE 0
#define MW_CONNECTIONINFO_XCPONWIFI_IPADDRESS codertarget.arduinobase.internal.getExternalModeMexArgs('Wifi')
#define MW_CONNECTIONINFO_XCPONWIFI_PORT 17725
#define MW_CONNECTIONINFO_XCPONWIFI_VERBOSE 0
#define MW_EXTMODE_CONFIGURATION Serial
#define MW_EXTMODE_COMPORTBAUD 921600
#define MW_EXTMODE_HOSTINTERFACE 0
#define MW_EXTMODE_SIGNALBUFFERSIZE 1000000.000000
#define MW_EXTMODE_RUNNING on
#define MW_RTOS Baremetal
#define MW_SCHEDULER_INTERRUPT_SOURCE 0
#define MW_RUNTIME_BUILDACTION 1
#define MW_RUNTIME_DISABLEPARALLELBUILD 0
#define MW_RUNTIME_FORCEBUILDSTATICLIBRARY 0
#define MW_HOSTCOMPORT_SET_HOST_COM_PORT 0
#define MW_HOSTCOMPORT_COM_PORT_NUMBER 1
#define MW_SIMULINKIO_ENABLE_SIMULINKIO 1
#define MW_OVERRUNDETECTION_ENABLE_OVERRUN_DETECTION 0
#define MW_OVERRUNDETECTION_DIGITAL_OUTPUT_TO_SET_ON_OVERRUN 13
#define MW_ANALOGINREFVOLTAGE_ANALOG_INPUT_REFERENCE_VOLTAGE 0.000000
#define MW_SERIAL_SERIAL0_BAUD_RATE 3
#define MW_SERIAL_SERIAL1_BAUD_RATE 3
#define MW_SERIAL_SERIAL2_BAUD_RATE 3
#define MW_SERIAL_SERIAL3_BAUD_RATE 3
#define MW_I2C_I2C0BUSSPEEDHZ 100000
#define MW_SPI_SPI_CLOCK_OUT_FREQUENCY 1
#define MW_SPI_SPI_MODE 0
#define MW_SPI_SPI_BITORDER 0
#define MW_SPI_SDSLAVESELECT 4.000000
#define MW_SPI_CANCHIPSELECT 9.000000
#define MW_ETHERNET_DISABLE_DHCP_ETHERNET 0
#define MW_ETHERNET_LOCAL_IP_ADDRESS 192.168.0.20
#define MW_ETHERNET_LOCAL_MAC_ADDRESS DE:AD:BE:EF:FE:ED
#define MW_WIFI_WIFI_HARDWARE -1
#define MW_WIFI_DISABLE_DHCP_WIFI 0
#define MW_WIFI_WIFI_IP_ADDRESS 192.168.1.20
#define MW_WIFI_WIFI_SSID yourNetwork
#define MW_WIFI_SET_WIFI_ENCRYPTION -1
#define MW_WIFI_WIFI_WEP_KEY D0D0DEADF00DABBADEAFBEADED
#define MW_WIFI_WIFI_WEP_KEY_INDEX 0
#define MW_WIFI_WIFI_WPA_PASSWORD secretPassword
#define MW_WIFI_WIFI_ESP8266_HW_SERIAL_PORT -1
#define MW_THINGSPEAK_ENABLE_CUSTOMSERVER 48
#define MW_THINGSPEAK_IP_ADDRESS 184.106.153.149
#define MW_THINGSPEAK_PORT 80
#define MW_CAN_CANBUSSPEED 10
#define MW_CAN_CANOSCILLATORFREQUENCY 1
#define MW_CAN_INTERRUPTPIN 2.000000
#define MW_CAN_ALLOWALLFILTER 0
#define MW_CAN_BUFFER0IDTYPE 0
#define MW_CAN_ACCEPTANCEMASK0_NOR 0
#define MW_CAN_ACCEPTANCEFILTER0_NOR 255
#define MW_CAN_ACCEPTANCEFILTER1_NOR 255
#define MW_CAN_ACCEPTANCEMASK0_EXT 0
#define MW_CAN_ACCEPTANCEFILTER0_EXT 255
#define MW_CAN_ACCEPTANCEFILTER1_EXT 255
#define MW_CAN_BUFFER1IDTYPE 0
#define MW_CAN_ACCEPTANCEMASK1_NOR 0
#define MW_CAN_ACCEPTANCEFILTER2_NOR 255
#define MW_CAN_ACCEPTANCEFILTER3_NOR 255
#define MW_CAN_ACCEPTANCEFILTER4_NOR 255
#define MW_CAN_ACCEPTANCEFILTER5_NOR 255
#define MW_CAN_ACCEPTANCEMASK1_EXT 0
#define MW_CAN_ACCEPTANCEFILTER2_EXT 255
#define MW_CAN_ACCEPTANCEFILTER3_EXT 255
#define MW_CAN_ACCEPTANCEFILTER4_EXT 255
#define MW_CAN_ACCEPTANCEFILTER5_EXT 255
#define MW_MODBUS_MODBUS_COMMS 0
#define MW_MODBUS_MODBUS_MODE 0
#define MW_MODBUS_MODBUS_SLAVEID 1
#define MW_MODBUS_MODBUS_CONFIGCOIL 49
#define MW_MODBUS_MODBUS_COILADDR 0
#define MW_MODBUS_MODBUS_COILNUM 1
#define MW_MODBUS_MODBUS_CONFIGINPUT 49
#define MW_MODBUS_MODBUS_INPUTADDR 0
#define MW_MODBUS_MODBUS_INPUTNUM 1
#define MW_MODBUS_MODBUS_CONFIGHOLDINGREG 49
#define MW_MODBUS_MODBUS_HOLDINGREGADDR 0
#define MW_MODBUS_MODBUS_HOLDINGREGNUM 1
#define MW_MODBUS_MODBUS_CONFIGINPUTREG 49
#define MW_MODBUS_MODBUS_INPUTREGADDR 0
#define MW_MODBUS_MODBUS_INPUTREGNUM 1
#define MW_MODBUS_MODBUS_MASTERTIMEOUT 100
#define MW_RS485_RS485_SERIAL 1
#define MW_RS485_RS485_BAUD 9600
#define MW_RS485_RS485_CONFIG 3
#define MW_RS485_RS485_DEPIN 8
#define MW_RS485_RS485_REPIN 9
#define MW_DISPLAY_ENABLECODEGEN 0
#define MW_DISPLAY_APPLAUNCHBUTTON 
#define MW_DATAVERSION 2016.02
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

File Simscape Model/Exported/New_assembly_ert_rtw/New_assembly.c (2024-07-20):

/*
 * File: New_assembly.c
 *
 * Code generated for Simulink model 'New_assembly'.
 *
 * Model version                  : 1.9
 * Simulink Coder version         : 9.5 (R2021a) 14-Nov-2020
 * C/C++ source code generated on : Sun Jan 14 08:03:38 2024
 *
 * Target selection: ert.tlc
 * Embedded hardware selection: Atmel->AVR
 * Code generation objectives: Unspecified
 * Validation result: Not run
 */

#include "New_assembly.h"
#include "New_assembly_private.h"
#include "New_assembly_dt.h"

/* Real-time model */
static RT_MODEL_New_assembly_T New_assembly_M_;
RT_MODEL_New_assembly_T *const New_assembly_M = &New_assembly_M_;
real_T rt_roundd_snf(real_T u)
{
  real_T y;
  if (fabs(u) < 4.503599627370496E+15) {
    if (u >= 0.5) {
      y = floor(u + 0.5);
    } else if (u > -0.5) {
      y = u * 0.0;
    } else {
      y = ceil(u - 0.5);
    }
  } else {
    y = u;
  }

  return y;
}

/* Model step function */
void New_assembly_step(void)
{
  real_T tmp_0;
  uint8_T tmp;

  /* MATLABSystem: '<Root>/Standard Servo Write' incorporates:
   *  Constant: '<Root>/Constant'
   */
  if (New_assembly_P.Constant_Value < 0.0) {
    tmp = 0U;
  } else if (New_assembly_P.Constant_Value > 180.0) {
    tmp = 180U;
  } else {
    tmp_0 = rt_roundd_snf(New_assembly_P.Constant_Value);
    if (tmp_0 < 256.0) {
      if (tmp_0 >= 0.0) {
        tmp = (uint8_T)tmp_0;
      } else {
        tmp = 0U;
      }
    } else {
      tmp = MAX_uint8_T;
    }
  }

  MW_servoWrite(0, tmp);

  /* End of MATLABSystem: '<Root>/Standard Servo Write' */

  /* External mode */
  rtExtModeUploadCheckTrigger(1);

  {                                    /* Sample time: [0.2s, 0.0s] */
    rtExtModeUpload(0, (real_T)New_assembly_M->Timing.taskTime0);
  }

  /* signal main to stop simulation */
  {                                    /* Sample time: [0.2s, 0.0s] */
    if ((rtmGetTFinal(New_assembly_M)!=-1) &&
        !((rtmGetTFinal(New_assembly_M)-New_assembly_M->Timing.taskTime0) >
          New_assembly_M->Timing.taskTime0 * (DBL_EPSILON))) {
      rtmSetErrorStatus(New_assembly_M, "Simulation finished");
    }

    if (rtmGetStopRequested(New_assembly_M)) {
      rtmSetErrorStatus(New_assembly_M, "Simulation finished");
    }
  }

  /* Update absolute time for base rate */
  /* The "clockTick0" counts the number of times the code of this task has
   * been executed. The absolute time is the multiplication of "clockTick0"
   * and "Timing.stepSize0". Size of "clockTick0" ensures timer will not
   * overflow during the application lifespan selected.
   */
  New_assembly_M->Timing.taskTime0 =
    ((time_T)(++New_assembly_M->Timing.clockTick0)) *
    New_assembly_M->Timing.stepSize0;
}

/* Model initialize function */
void New_assembly_initialize(void)
{
  /* Registration code */
  rtmSetTFinal(New_assembly_M, 10.0);
  New_assembly_M->Timing.stepSize0 = 0.2;

  /* External mode info */
  New_assembly_M->Sizes.checksums[0] = (3895108551U);
  New_assembly_M->Sizes.checksums[1] = (2467505585U);
  New_assembly_M->Sizes.checksums[2] = (2070691188U);
  New_assembly_M->Sizes.checksums[3] = (1019155614U);

  {
    static const sysRanDType rtAlwaysEnabled = SUBSYS_RAN_BC_ENABLE;
    static RTWExtModeInfo rt_ExtModeInfo;
    static const sysRanDType *systemRan[2];
    New_assembly_M->extModeInfo = (&rt_ExtModeInfo);
    rteiSetSubSystemActiveVectorAddresses(&rt_ExtModeInfo, systemRan);
    systemRan[0] = &rtAlwaysEnabled;
    systemRan[1] = &rtAlwaysEnabled;
    rteiSetModelMappingInfoPtr(New_assembly_M->extModeInfo,
      &New_assembly_M->SpecialInfo.mappingInfo);
    rteiSetChecksumsPtr(New_assembly_M->extModeInfo,
                        New_assembly_M->Sizes.checksums);
    rteiSetTPtr(New_assembly_M->extModeInfo, rtmGetTPtr(New_assembly_M));
  }

  /* data type transition information */
  {
    static DataTypeTransInfo dtInfo;
    (void) memset((char_T *) &dtInfo, 0,
                  sizeof(dtInfo));
    New_assembly_M->SpecialInfo.mappingInfo = (&dtInfo);
    dtInfo.numDataTypes = 15;
    dtInfo.dataTypeSizes = &rtDataTypeSizes[0];
    dtInfo.dataTypeNames = &rtDataTypeNames[0];

    /* Block I/O transition table */
    dtInfo.BTransTable = &rtBTransTable;

    /* Parameters transition table */
    dtInfo.PTransTable = &rtPTransTable;
  }

  /* Start for MATLABSystem: '<Root>/Standard Servo Write' */
  MW_servoAttach(0, 8);
}

/* Model terminate function */
void New_assembly_terminate(void)
{
  /* (no terminate code required) */
}

/*
 * File trailer for generated code.
 *
 * [EOF]
 */
